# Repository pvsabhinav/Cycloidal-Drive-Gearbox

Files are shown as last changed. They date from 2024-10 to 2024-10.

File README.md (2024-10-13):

# Cycloidal-Drive-Gearbox

**Cycloidal Drive Gearbox Info:**
- 10:1 Gear ratio
- Best used in robotics applications, or applications where low speed and high torque are required
- Estimated total cost to build gearbox is $85 (note: this does not include the motor)
- Important note: I made most of my parts in mm as the motor I found which was a good fit had its dimensions in mm. Most of the parts I bought are also in mm, especially the ones that are related with the motor. 

**Parts List**
- 3D printed parts (all parts to print are in the files above)
- I used an Eaglepower (kv90) brushless motor, but the motor case file can be edited to adapt to any motor
- 2 55x72x9 mm bearing
- M4 Brass Heat-Set threaded inserts (try to get the knurled ones)
- 2 1/2x1-1/8x5/16 **in** bearing (note: this bearing is in inches, not mm, as I could not find a bearing in mm that fit my needs)
- 30 4x8x3 mm bearings
- Assorted M4 Bolts and nuts. [Here](https://www.amazon.com/iExcell-Stainless-Socket-Button-Assortment/dp/B08Z7GQVQ9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) is a set of bolts I reccomend

[**How To Build (Video)**](https://drive.google.com/file/d/1M7n9Yk40CGF0MDWzt1fGfLzIRFFRU5Fq/view?usp=sharing)

**Acknowledgments**
- Maximilian Schommer - [Onshape FeatureScript for Cycloidal Gears](https://cad.onshape.com/documents/347e6a9ae9d0992f4b101a70/w/d85d62ab1c292cc0d3314104/e/39a63585c0c29cabbfacb536)
- Not an Engineer - [Video](https://www.youtube.com/watch?v=YFJJkZm796I) helped me better understand the how cycloidal drive gearboxes worked

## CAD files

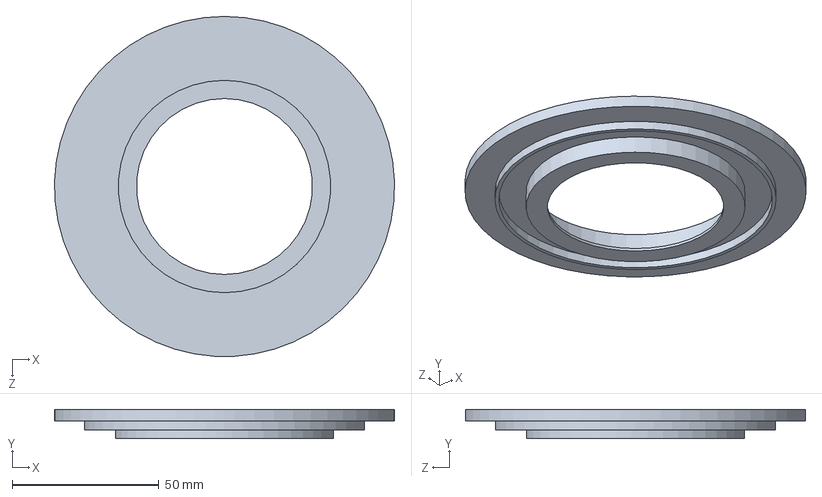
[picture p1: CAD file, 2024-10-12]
Solidworks Files/TopBearingHolder.SLDPRT
115.9 x 10.0 x 116.0 mm

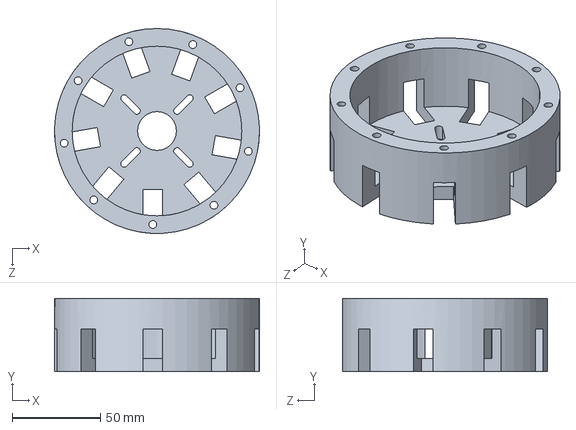
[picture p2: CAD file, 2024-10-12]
Solidworks Files/MotorCase.SLDPRT
116.0 x 41.5 x 116.0 mm

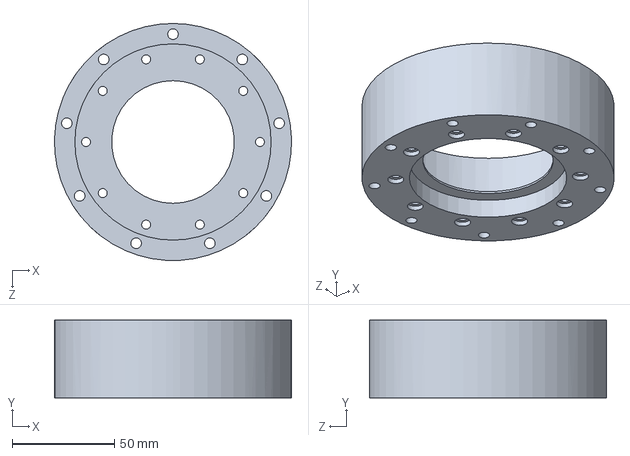
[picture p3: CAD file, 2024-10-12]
Solidworks Files/Gear Case.SLDPRT
115.9 x 38.1 x 116.0 mm

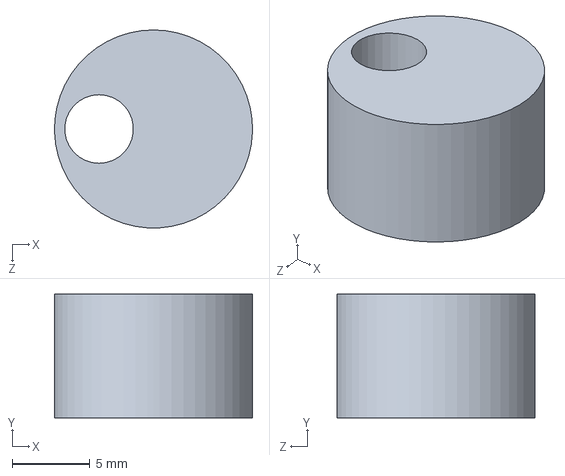
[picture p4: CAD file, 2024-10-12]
Solidworks Files/Shaft(Top).SLDPRT
12.7 x 7.94 x 12.7 mm

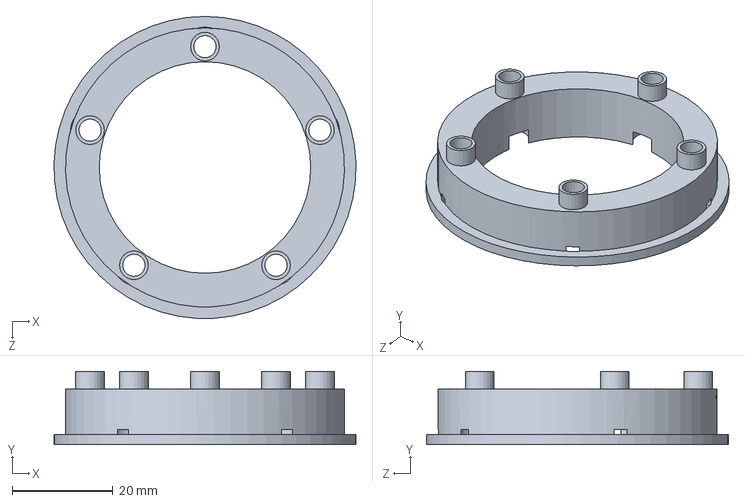
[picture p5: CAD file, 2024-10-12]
Solidworks Files/Inner Pin Holder.SLDPRT
60.0 x 14.5 x 60.0 mm

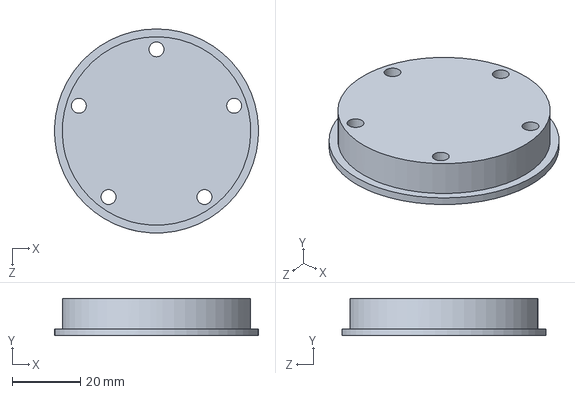
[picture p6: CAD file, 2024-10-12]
Solidworks Files/TopPinHolder.SLDPRT
60.0 x 11.0 x 60.0 mm

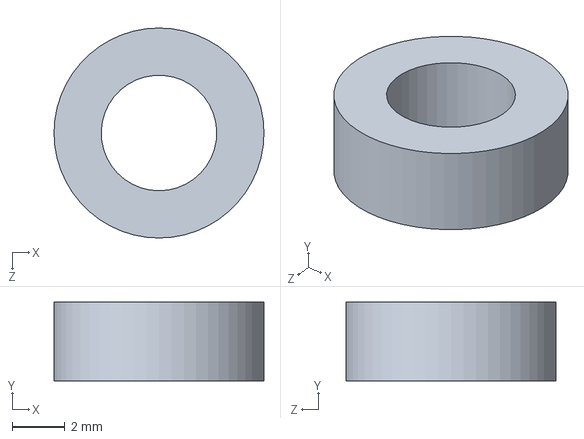
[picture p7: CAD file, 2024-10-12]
Solidworks Files/Spacer.SLDPRT
8.00 x 3.00 x 8.00 mm

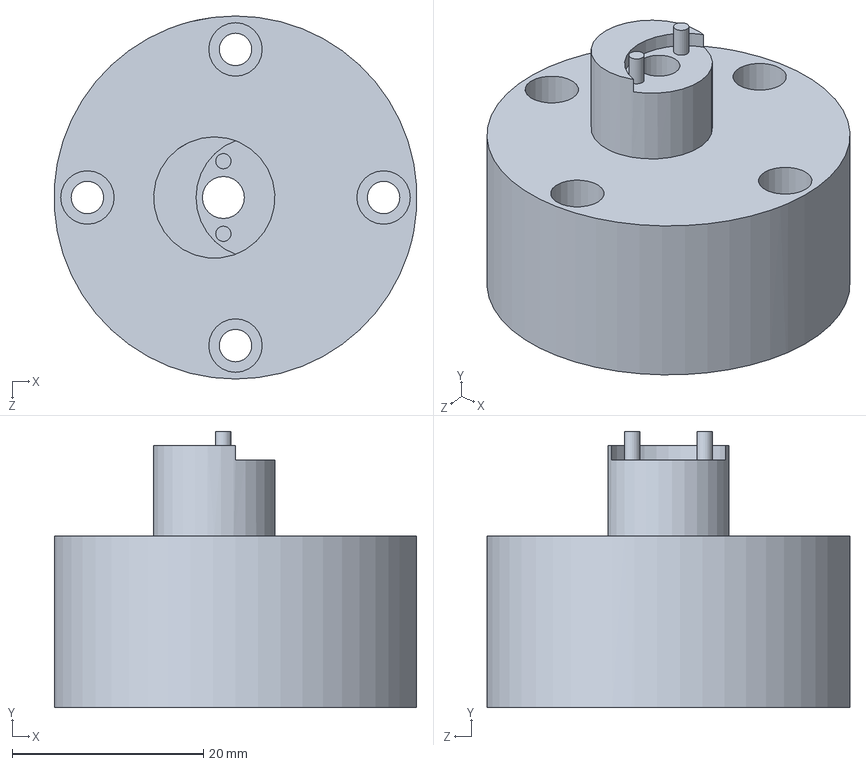
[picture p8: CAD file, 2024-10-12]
Solidworks Files/Shaft(Bottom).SLDPRT
37.9 x 28.9 x 38.0 mm

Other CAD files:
Solidworks Files/Cycloidal Gear.sldprt
STL Files/Cycloidal Gear.stl
STL Files/Gear Case.STL
STL Files/Inner Pin Holder.STL
STL Files/MotorCase.STL
STL Files/Shaft(Bottom).STL
STL Files/Shaft(Top).STL
STL Files/Spacer.STL
STL Files/Top Bearing Holder.STL
STL Files/Top Pin Holder.STL

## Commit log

2024-10-12 Added solidworks files
    [Cycloidal Gear.sldprt, Gear Case.SLDPRT, Inner Pin Holder.SLDPRT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]
2024-10-12 Added STL files
    [Cycloidal Gear.stl, Gear Case.STL, Inner Pin Holder.STL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]
